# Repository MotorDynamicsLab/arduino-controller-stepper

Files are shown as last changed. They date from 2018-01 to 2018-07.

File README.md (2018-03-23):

# arduino-controller-stepper
This repository contains sample code for the ARC-S (ARduino-Controller-Stepper) board. 
The code provided can be used as is or modified freely to suit your own application.
Contained are two projects:
- the "arc-s" directory contains main arc-s sample code which the board comes shipped with. It contains a arcs library that can be easily ported to other projects.
- the "current-setter" directory contains a project used to help configure the current limit of the stepper driver.

## Arduino - Stepper Driver Interface
ARC-S uses pins which are unused by the Arduino Mega to control the stepper driver (except for STEP pin). 
This allows ARC-S to be used as an ordinary Arduino Mega if needed. The following table lists the pin connections between
the Arduino microcontroller (ATmega2560) and stepper driver (A4988):  

| A4988  | ATmega2560 |
|---|---|
| STEP | PL3 (D46)  |
| DIR | PJ3 |
| ENABLE | PJ2 |
| MS1 | PJ5 |
| MS2 | PJ6 |
| MS3 | PJ7 |
| VREF | PH7* |

\* _PH7 is used to switch between normal current and low current mode. Two trimpots on the board are used to adjust
the current limit in these two modes._ 

### Pin Manipulation
Manipulating pins in the stepper driver interface requires some simple register and bit manipulation:

To setup a pin as ouput use:
```c
DDRx |= (1<<y);
```
where x is the port and y is the pin offset. For example, setting up ENABLE pin: 
```c
DDRJ |= (1<<2);
```
To set a pin to logic high use: 
```c
PORTx |= (1<<y);
```
For example, setting STEP to logic high: 
```c
PORTL |= (1<<3);
```
Similarly, to clear a pin to logic low use:
```c
PORTx &= (~(1<<y));
```
For example, clearing MS1:
```c
PORTJ &= (~(1<<5));
```

### ENABLE Pin
The ENABLE pin switches the stepper drive on or off. 
The polarity of the pin is active low, so the stepper drive is enabled when the pin is logic low and is disabled when the pin is logic high. 
When the enable pin is not configured, a pull-up circuit on the PCB ensures that the stepper driver stays disabled by default.

### STEP & DIR Pins
The stepper drive moves the motor by one step when the STEP pin transitions from logic low to logic high (a.k.a. rising edge). 
The size of each step is controlled by the microstep settings. Thus the user can control the distance in which the motor moves by controlling the number of square wave pulses on the STEP pin as well as the speed of the motor by varying the frequency of the squarewaves. 
Changing the logic level on the DIR pin will change the direction of movement from subsequent STEP signals.

### Microstep Setting
The combined logic value of pins MS1, MS2, MS3 determines the microstep setting of the stepper drive. 
The following table defines possible combinations of MS1, MS2, MS3 and their corresponding microstep setting:

|  MS1 | MS2  | MS3  | Microstep Resolution | Steps/Rev (200 step motor) |
|---|---|---|---|---|
| LOW  | LOW  | LOW  | Full step | 200 steps/rev |
| HIGH | LOW  | LOW  | Half step | 400 steps/rev |
| LOW  | HIGH | LOW  | 1/4 step | 800 steps/rev |
| HIGH | HIGH | LOW  | 1/8 step | 1600 steps/rev |
| HIGH | HIGH | HIGH | 1/16 step | 3200 steps/rev |

### Current Mode Switching
The ARC-S board contains a circuit that allows the application to switch between two current modes. Each current mode is adjustable with a trimpot on the board.
Toggling the value of pin PH7 switches between the two current modes. 
- Setting PH7 to logic high leaves the stepper driver in "normal current" mode. 
- Clearing PH7 to logic low switches the stepper driver to "low current" mode.
- The stepper driver remains in "normal current" mode if PH7 is left unconfigured.

## Simple Control Panel
ARC-S integrates a simple pushbutton and switch control panel. The control panel contains 3 momentary pushbuttons (UP, DOWN, START/STOP)
and a single switch (CW/CCW). These buttons and switches are linked to normal Arduino digital I/O pins and can be read using `digitalRead()`. 

| Button | Arduino Pin |
|---|---|
| UP | 22 |
| DOWN | 24 |
| START/STOP | 26 |
| CW/CCW | 28 |

- For the pushbuttons (UP, DOWN, START/STOP), pressing the button connects the corresponding Arduino pin to ground (logic LOW); releasing the button leaves the pin unconnected (floating). 
- For the switch (CW/CCW), toggling to "CCW" connects the Arduino pin to ground while toggling to "CW" leaves the pin unconnected.
- In order to use the control panel properly, the pins should be configured with `pinMode(x, INPUT_PULLUP)`. This enables the internal pullup and makes the pins read logic high when they are unconnected externally.

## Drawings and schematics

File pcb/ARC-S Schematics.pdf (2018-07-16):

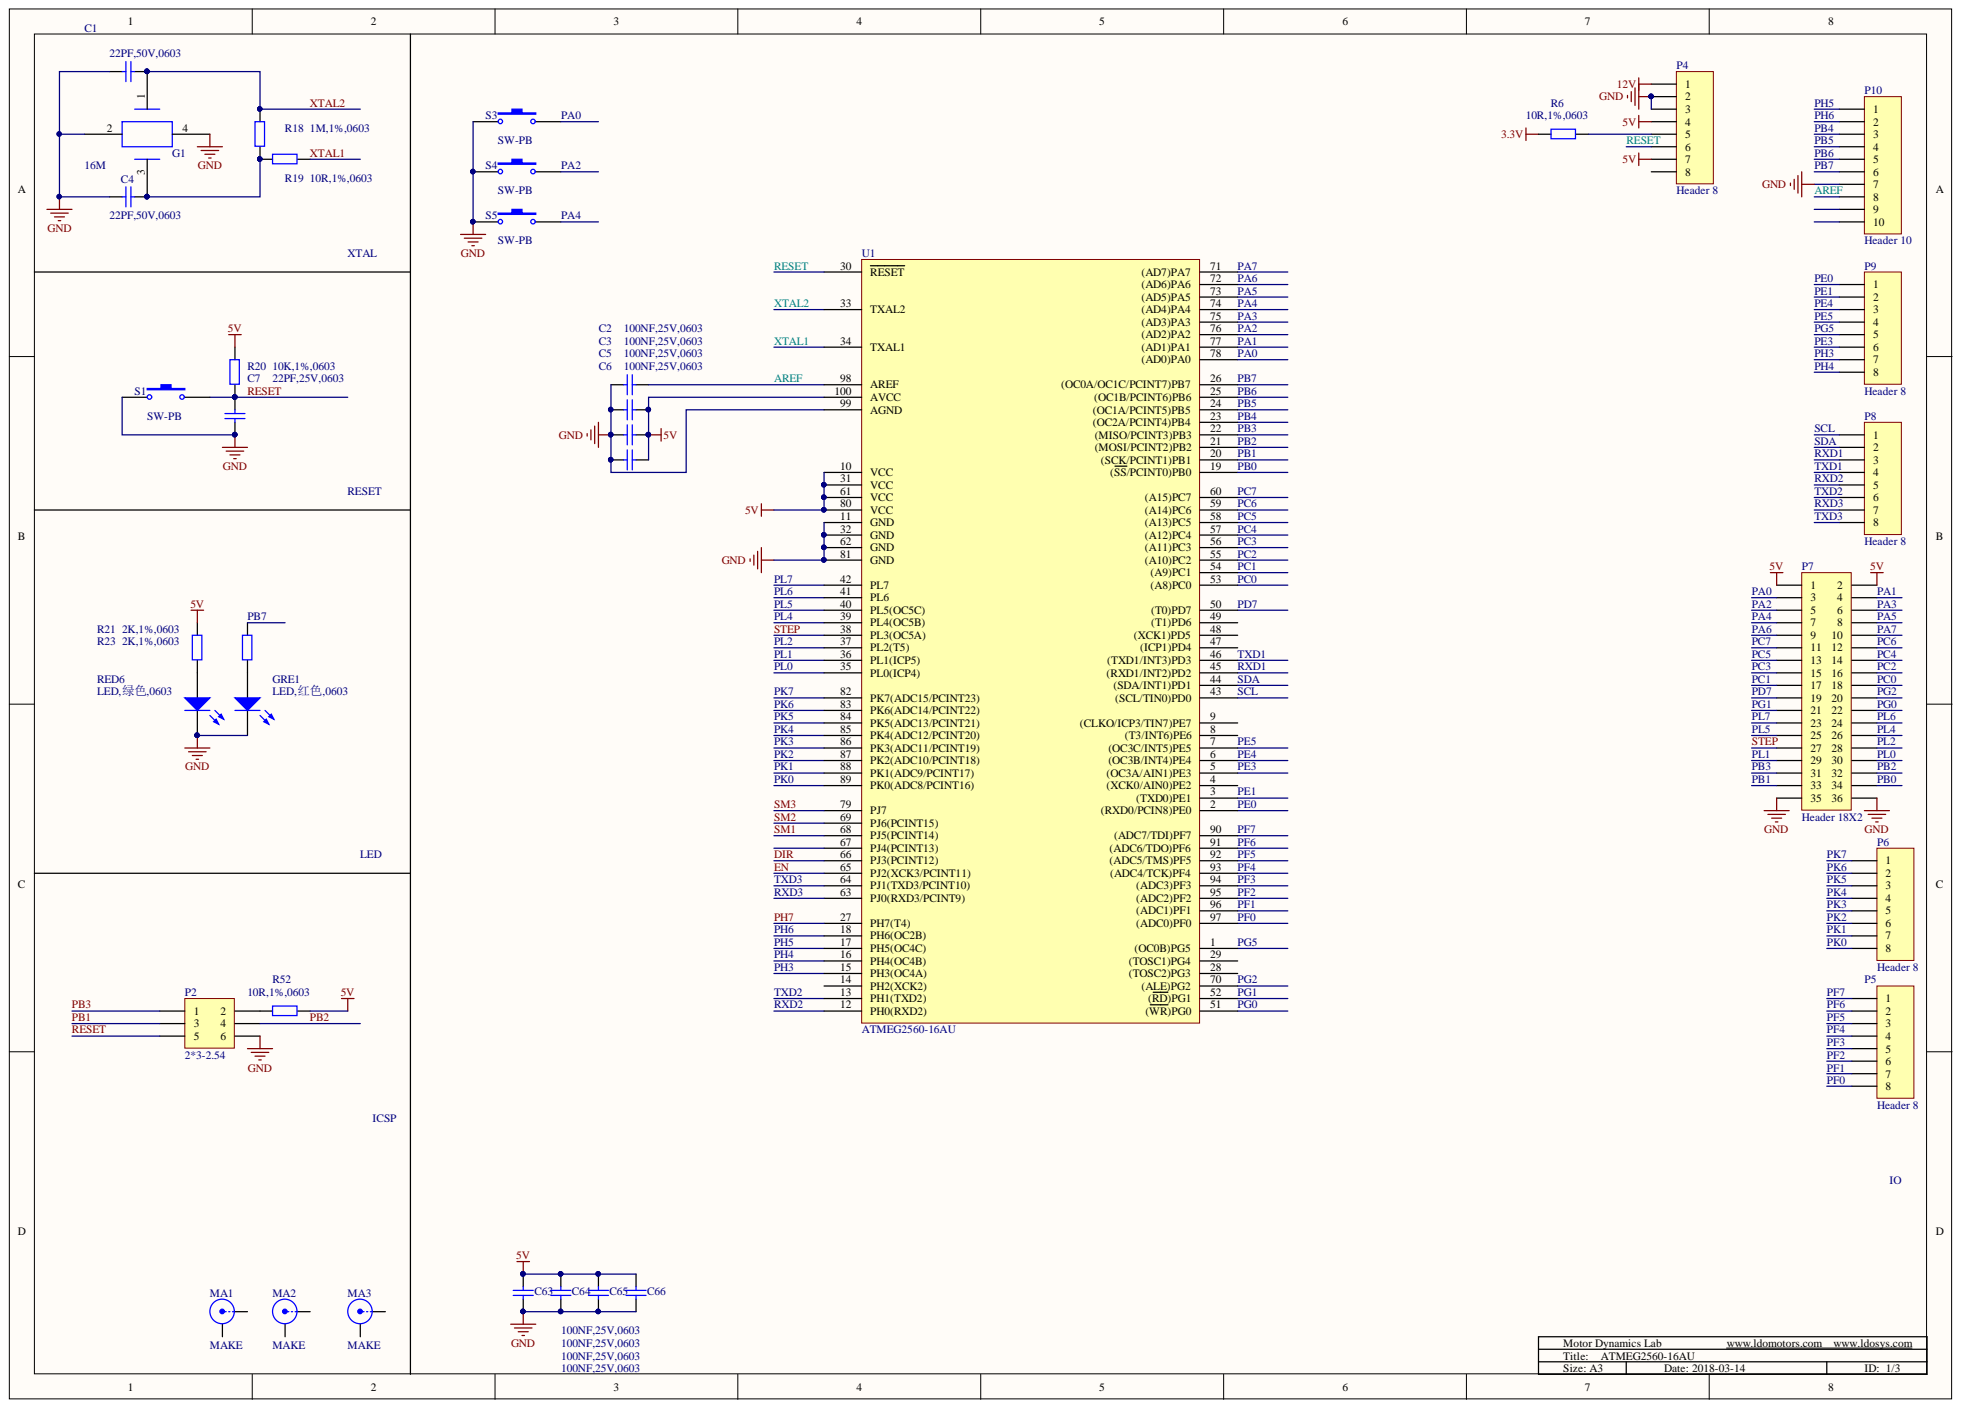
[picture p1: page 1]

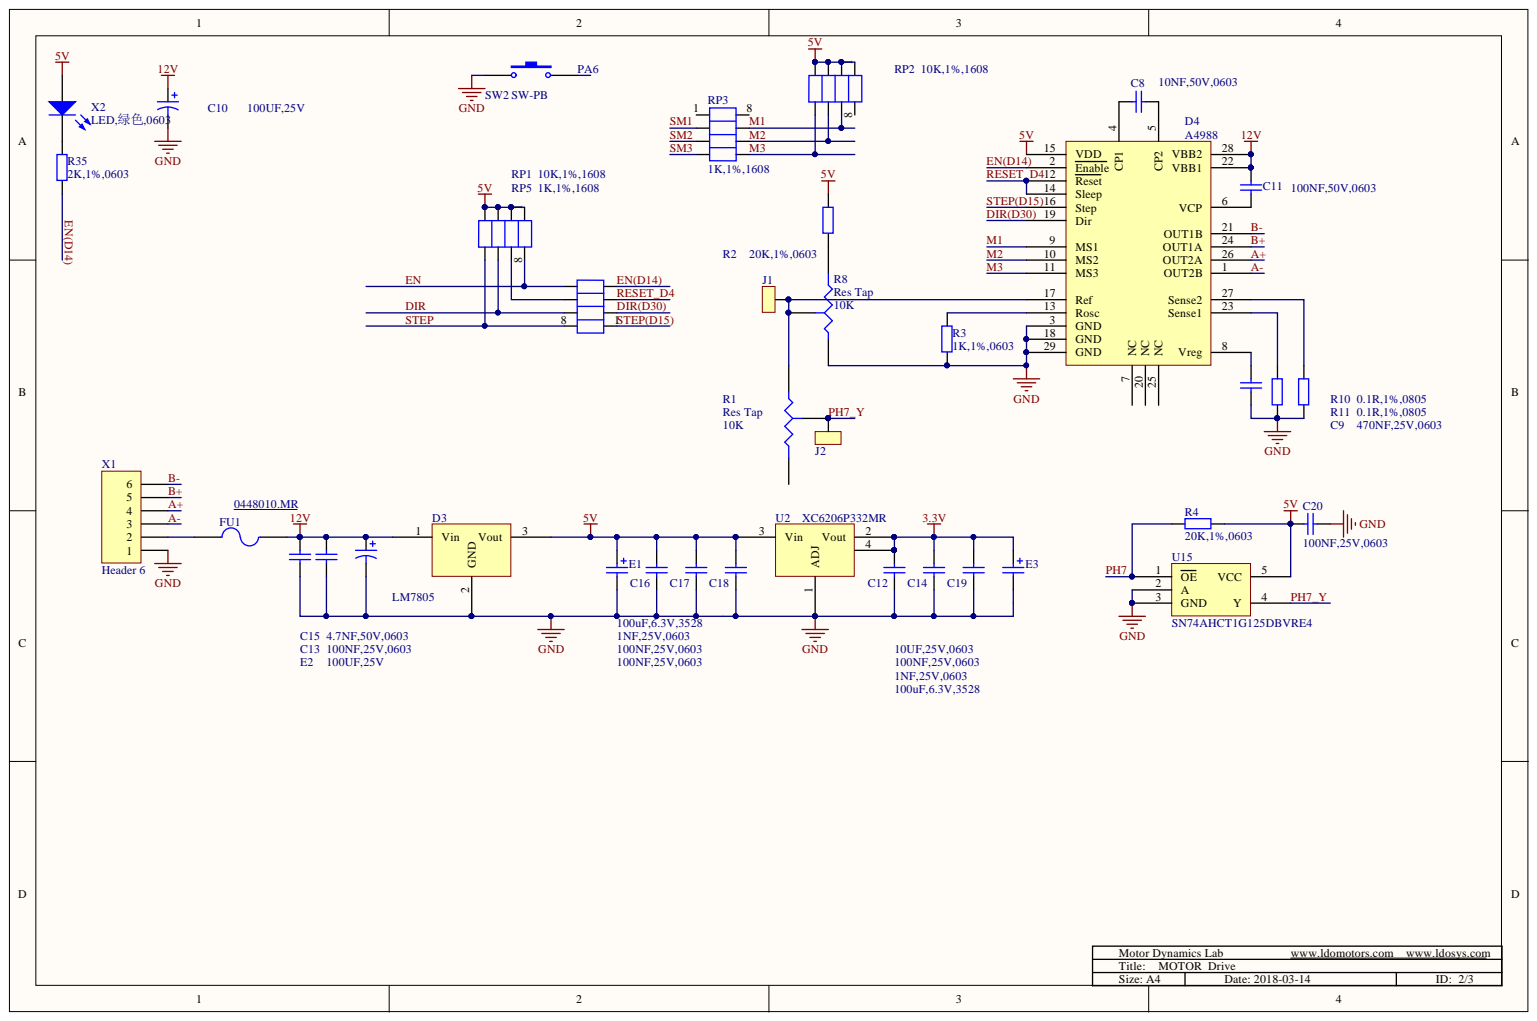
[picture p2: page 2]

M1
M2

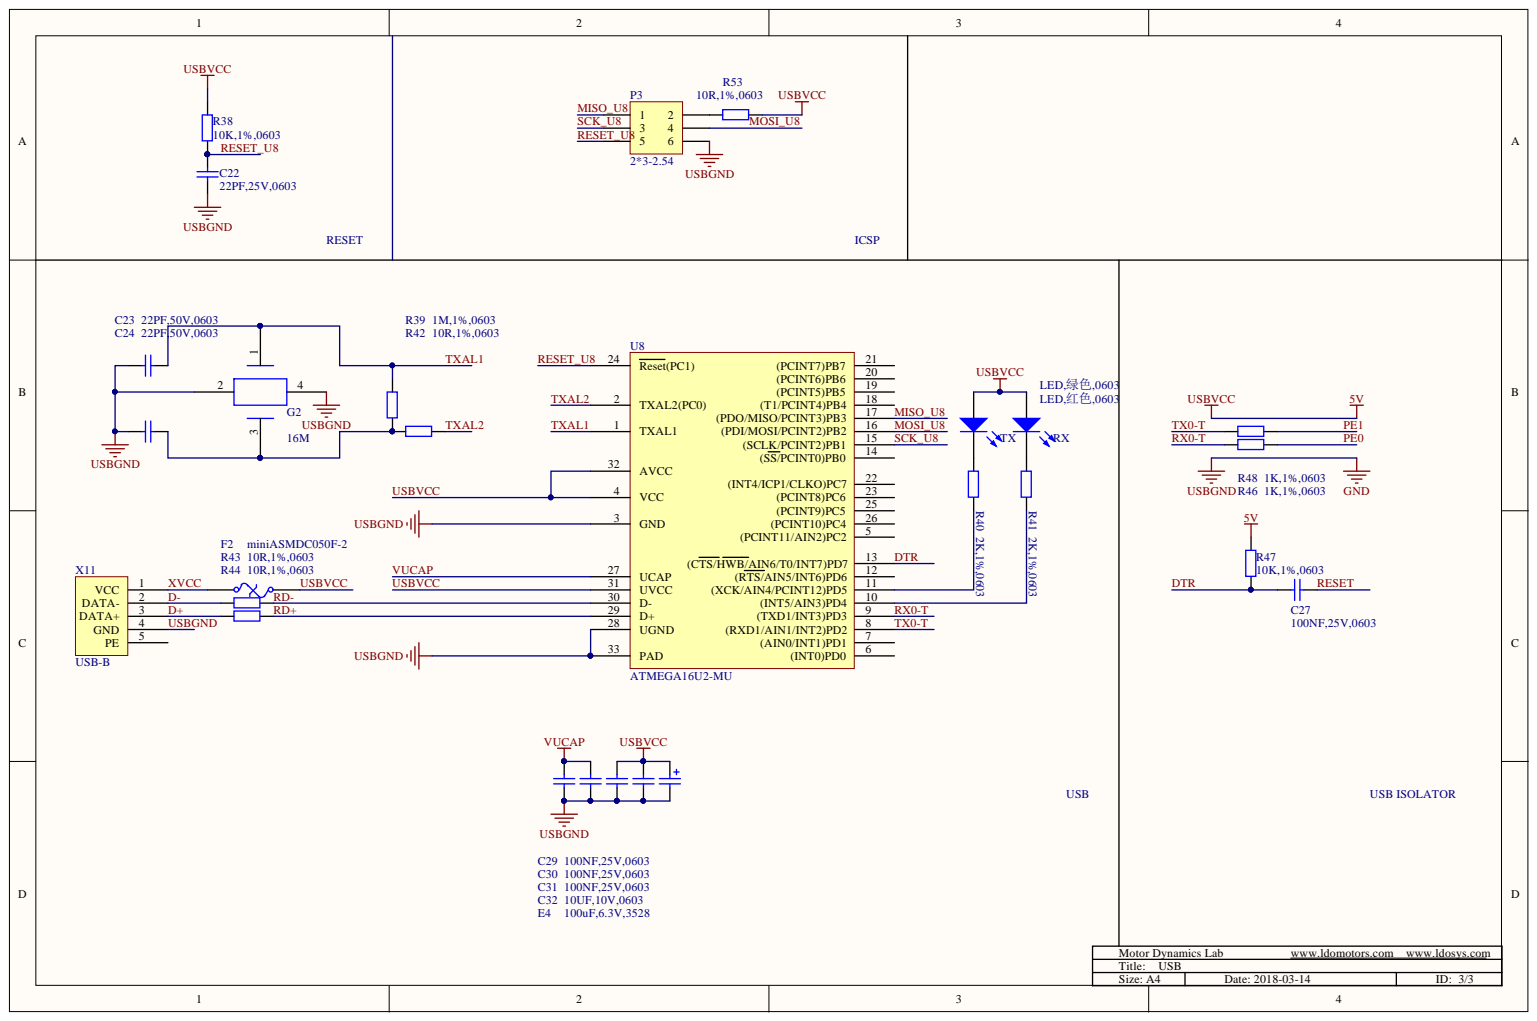
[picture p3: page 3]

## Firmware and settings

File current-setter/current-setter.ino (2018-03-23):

//###########################################################################
// current-setup.ino
// Use this program to adjust the current setting on the stepper driver.
//
// - Pressing the "START/STOP" button toggles the enable state of 
//   the stepper driver.
// - Pressing the "DOWN" button toggles between normal current mode
//   and low current mode.
//
// $Copyright: Copyright (C) LDO Systems
//###########################################################################
#define DOWN_PIN 24
#define START_PIN 26

#define setup_vref() (DDRH |= 1 << 7)
#define vref_normal() (PORTH |= 1 << 7)
#define vref_low() (PORTH &= (~(1 << 7)))

#define setup_ena() (DDRJ |= 1 << 2)
#define enable_stepper() (PORTJ &= (~(1 << 2)))
#define disable_stepper() (PORTJ |= 1 << 2)

const int debounceDelay = 100;

struct Button
{
  int pinNum;
  int state;
  int lastState;
  unsigned long lastDebounceTime;

  Button(int pin) :
    pinNum(pin),
    lastDebounceTime(0)
  {}
};

Button downBtn(DOWN_PIN);
Button startBtn(START_PIN);
bool isStepperEnabled = false;
bool isVrefNormalState = true;

void setup()
{
  //setup A4988 pins
  disable_stepper();
  vref_normal();
  setup_ena();
  setup_vref();

  //setup buttons
  setupButton(downBtn);
  setupButton(startBtn);
}


void loop() {
  //check if DOWN button changed
  if (checkButton(downBtn))
  {
    //switch between low and high current mode
    if (LOW == downBtn.state)
    {
      if (isVrefNormalState)
      {
        vref_low();
        isVrefNormalState = false;
      }
      else
      {
        vref_normal();
        isVrefNormalState = true;
      }
    }
  }

  //check if START/STOP button changed
  if (checkButton(startBtn))
  {
    //switch between enable and disable state
    if (LOW == startBtn.state)
    {
      if (isStepperEnabled)
      {
        disable_stepper();
        isStepperEnabled = false;
      }
      else
      {
        enable_stepper();
        isStepperEnabled = true;
      }
    }
  }
}


//Configures the button and initializes internal states
void setupButton(Button& btn)
{
  pinMode(btn.pinNum, INPUT_PULLUP);
  int init_reading = digitalRead(btn.pinNum);
  
  btn.state = init_reading;
  btn.lastState = init_reading;
}


//Checks and updates the state of the button
//returns true if state has changed
bool checkButton(Button& btn)
{
  bool stateChanged = false;
  int reading = digitalRead(btn.pinNum);

  if (reading != btn.lastState)
  {
    btn.lastDebounceTime = millis();
  }

  if ( (millis() - btn.lastDebounceTime) > debounceDelay)
  {
    if (reading != btn.state)
    {
      btn.state = reading;
      stateChanged = true;
    }
  }

  btn.lastState = reading;
  
  return stateChanged;
}

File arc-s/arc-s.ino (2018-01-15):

#include "arcs.h"
#define DIR 28
#define SPEED_UP 22
#define SLOW_DOWN 24
#define STOP_START 26
#define DELLAY 100

Arcs arcs;
bool dirState;
bool isMotorRun = false;
int32_t speed = 1000;

void setup() {
  // put your setup code here, to run once:
  //nitialize the pin
  pinMode(DIR,INPUT);
  digitalWrite(DIR,HIGH);
  
  pinMode(SPEED_UP,INPUT);
  digitalWrite(SPEED_UP,HIGH);
  
  pinMode(SLOW_DOWN,INPUT);
  digitalWrite(SLOW_DOWN,HIGH);
  
  pinMode(STOP_START,INPUT);
  digitalWrite(STOP_START,HIGH);
  
  //Configure subdivision and steps as well as initial speed and the number of motor steps and subdivisions
  arcs.initialize(200,16);
  
  //Check the direction before starting
  dirState = digitalRead(DIR);
  if(dirState)
    arcs.setDir(Arcs::ARCS_REVERSE);
  else
    arcs.setDir(Arcs::ARCS_FORWARD);

  arcs.setSpeed(speed);
}

void loop() {
  // put your main code here, to run repeatedly:
  //change direction
  if( dirState != digitalRead(DIR) )
  {
	//Judge the running status, if it is running, stop and then change the direction
    dirState = digitalRead(DIR);
    if(isMotorRun)
        arcs.stopMotor();
    if( debounce(DIR) )
    {
        arcs.setDir(Arcs::ARCS_FORWARD);
        Serial.println("ARCS_FORWARD");
    }
    else
    {
        arcs.setDir(Arcs::ARCS_REVERSE);
        Serial.println("ARCS_REVERSE");
    }
    if(isMotorRun)
        arcs.moveMotor(); 
    delay(10);
  }

  //accelerate
  if(!digitalRead(SPEED_UP))
  {
    if( debounce(SPEED_UP) )
	{
		speed += 10;
		arcs.setSpeed(speed);
	}
    delay(DELLAY);
  }

  //slow down
  if(!digitalRead(SLOW_DOWN))
  {
    if( debounce(SLOW_DOWN) )
	{
		speed -= 10;
    if(speed <= 0)
      speed = 1;
		arcs.setSpeed(speed);
	}
    delay(DELLAY);
  }

  //Start and stop
  if(!digitalRead(STOP_START))
  {
    if( debounce(STOP_START) )
    {
      while( !digitalRead(STOP_START) );
      isMotorRun = !isMotorRun;
      if(isMotorRun)
		      arcs.moveMotor();
      else
        arcs.stopMotor();
    }
	//Waiting for the button to release, to prevent continuous switching in an operation
    delay(DELLAY);
  }
}


///Eliminate button jitter
bool debounce(uint8_t pin)
{
  delay(10);
  if(digitalRead(pin))
    return false;
   else
    return true;
}

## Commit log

2017-12-28 添加了Gpio模块，通过了测试，可以避开GPIO映射表直接配置和控制GPIO 搭建了arc的基本结构
2018-01-04 完成了编写和测试，接下来添加加速控制部分，使电机的加速和减速更平稳
2018-01-05 将之前的比较输出模式改为了快速PWM模式，该模式下有双缓冲，在变频时，波形稳定，现在转速可以超过一千转
2018-01-09 完成了基本功能的测试
2018-01-10 修复了停机状态下换向会启动电机的bug
2018-01-11 按照要求进行了修改，现在准备删除Gpio的两个文件
2018-01-11 将Gpio中要使用的部分移到了arc类中，删除了Gpio类和两个文件；另外，设置加速度的函数没有修改，原因是本身就不能精确的控制加速度，意义不大，目前的接口能更精确的控制变速过程的速度变化
2018-01-11 减少了除法的使用，更改了设置加速度的函数
2018-01-12 修复了速度减小到极限时，突然变快，设置初始速度很小时，开机不能转动，加速才能动
2018-01-12 合并了设置线数的函数和初始化的函数
2018-01-12 增加了停止转动时调速功能
2018-01-15 完成了运行指定的距离
2018-01-15 修改了函数名
2018-03-23 add standalone project current-setter.ino, used for setting stepper driver current
2018-07-16 add schematics and source files of PCB
    [ARC-S-MCU.SchDoc, ARC-S-MOTOR.SchDoc, ARC-S-USB.SchDoc]
